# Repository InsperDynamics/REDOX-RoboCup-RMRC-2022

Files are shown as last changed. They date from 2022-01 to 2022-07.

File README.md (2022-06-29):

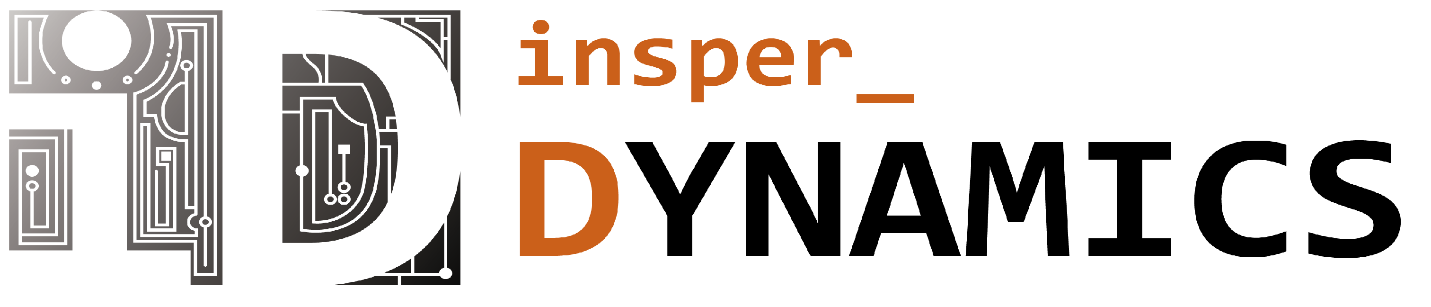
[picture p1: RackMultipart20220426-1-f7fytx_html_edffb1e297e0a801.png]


# Rapidly Manufactured Robot Challenge

# Robocup Rescue 2022

Arthur Martins de Souza Barreto, Enricco Gemha

Felipe Catapano Emrich Melo, Rafael Eli Katri.

April 2022

# Gratitude

Before everything, we want to express our gratitude for some people and organization, without their help we could not achieve everything we already did and still going. In special, Carlos, Felipe Catapano&#39;s father, where he had the initial insight and gave his house for our fist meetings.

We also would like to a huge thank you for our intuition, Insper, they helped us a lot when we need to find a place to train, have our meetings and principally, helped us to pay the cost from our travel to Robocup.

The following names helped us, directly or indirectly, to be the robotics team and build our robot. Thank you, Miranda, Raul, Alicia, Nilson, all laboratorian technical and our family for giving us support.

# About us

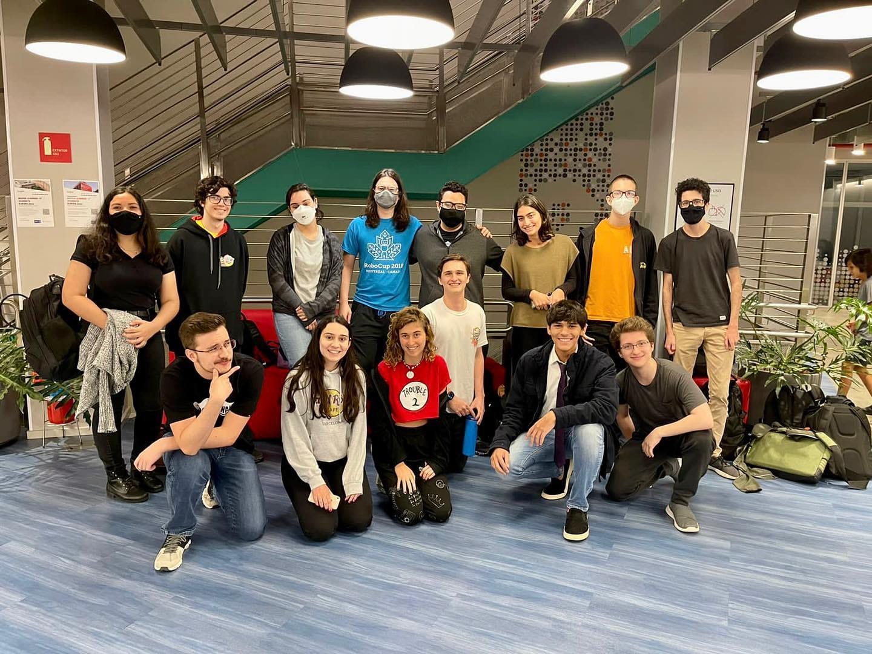
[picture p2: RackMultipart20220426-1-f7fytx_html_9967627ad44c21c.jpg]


We are a Brazilian team, from São Paulo, São Paulo. We born last year, with 3 students from Computer Engineer, two of them already had participate from Robocup, 4 and 2 times respectively, the other is a visionary.

After some hard work we became an official robotics team from our College, Insper, and today we are Insper Dynamics. Our group have students from different courses, Administration, Mechatronics Engineer, Mechanic Engineer, and Computer Engineer. Today we are 15, and still growing up.

## Our Social Medias

- Linkedin:

[https://www.linkedin.com/company/insperdynamics/mycompany/?viewAsMember=true](https://www.linkedin.com/company/insperdynamics/mycompany/?viewAsMember=true)

- Instagram:

[https://www.instagram.com/insper\_dynamics/](https://www.instagram.com/insper_dynamics/)

- Email:

[insperdynamics@gmail.com](mailto:insperdynamics@gmail.com)

- Github:

[https://github.com/InsperDynamics](https://github.com/InsperDynamics)

# Abstract

Our objective is to build a robot capable to get in dangerous ambientes, after natural disasters, places where the human would not be able to go, like a building after an earthquake.

The robot also be able to identify some images to take some actions, if he identifies a symbol of a specific warning, be able to handle it and take the correct action.

The robot is semi-autonomous, at a fist moment he going to be controlled by a remote control, being guide by the image from his camera, and at the same time, he will be mapping the ambient with a laser scanner. With the time pass, he will be able to be autonomous and take his own decision without the human interference.

Also, all the robots were imagined to be fast reproduced, his parts were designed and printed or manufactured, always thinking in how fast we can do it and the better way we can do it.

# Introduction

The world is changing fast, and day after day better solutions comes up. Ten years ago, we had an idea from autonomous cars, self-driving. However, nowadays, we got some cars capable to do that, man is always improving something.

With it in mind, Robocup was born to incentive students under the study from robotics and technology, AI development, everything that would be able to help humankind.

The Rapidly Manufactured Robot Challenge is a category from Robocup, with the goal to build a fast robot make and at the same time, a robot capable to help ser human, going into dangerous places where the man would suffer life risk.

This challenge takes us, Insper Dynamics team to think a lot about some strategies and the results is everything under this paper. For this competition, our team have four members, Arthur, Felipe, Antônio and Rafael, all from 3rd semester at Computer Engineer. The first two students acted as team leaders, teaching everything the group needed, both have 6 participations at Robocup if we some of them. Due we be a new team, we had no teacher helping us yet, but we got great results and have a big expectation on competition.

# Robot

Our robot has all the parts made by us, the body, the arm, the wells, the PCB. The next lines are going to clarify how we imagine and made every part.

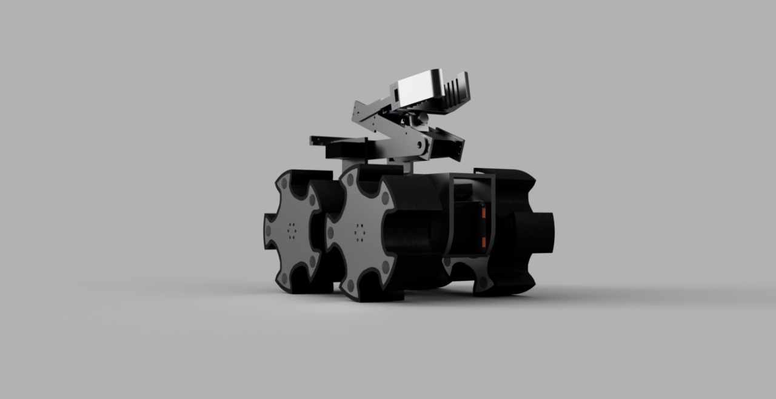
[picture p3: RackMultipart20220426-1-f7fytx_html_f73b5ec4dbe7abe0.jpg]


## Structure

The robot was designed to have two main bodies, independent one from another.

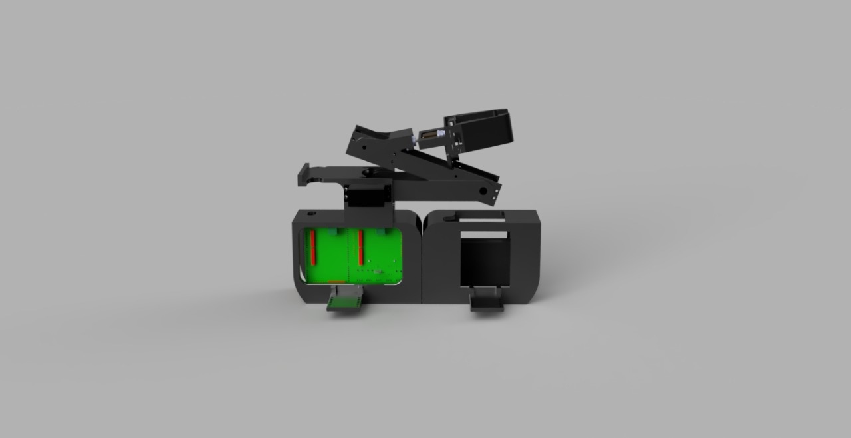
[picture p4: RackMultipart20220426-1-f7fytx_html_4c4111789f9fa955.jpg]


The front and back parts are free to twist around the axis of a central bearing, up to 30 degrees to each side (limited by a cental locking piece). This was done to allow the robot to always have all wheels in contact with the ground. When the robot finds an obstacle that makes a wheel lift, the robot twists, adjusting for the format of the field and continuing its task.

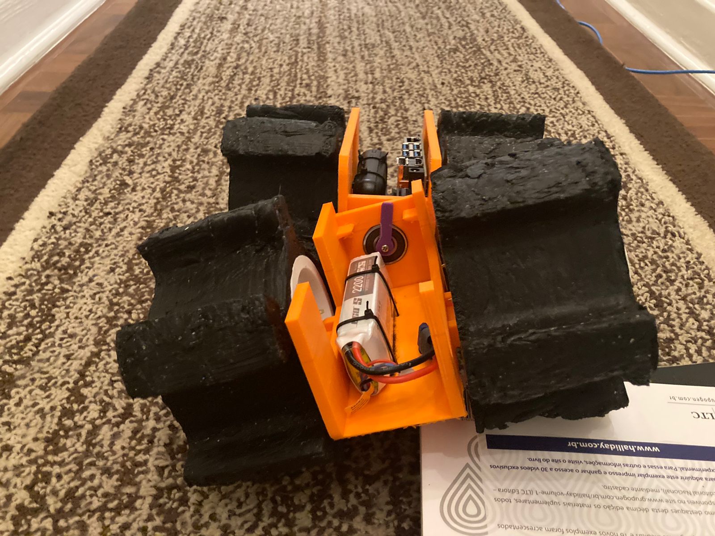
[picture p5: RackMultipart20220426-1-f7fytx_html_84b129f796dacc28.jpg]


On its chassis, we got those two parts, and inside them we placed the following components inside:

- Lipo Battery
- Arduino Mega
- Jetson Nano
- Motor Driver
- Power Bank
- Our PCB

We got two different power sources, one destined for actuators and the other for boards and sensors. This way we avoid interference from low battery under both parts.

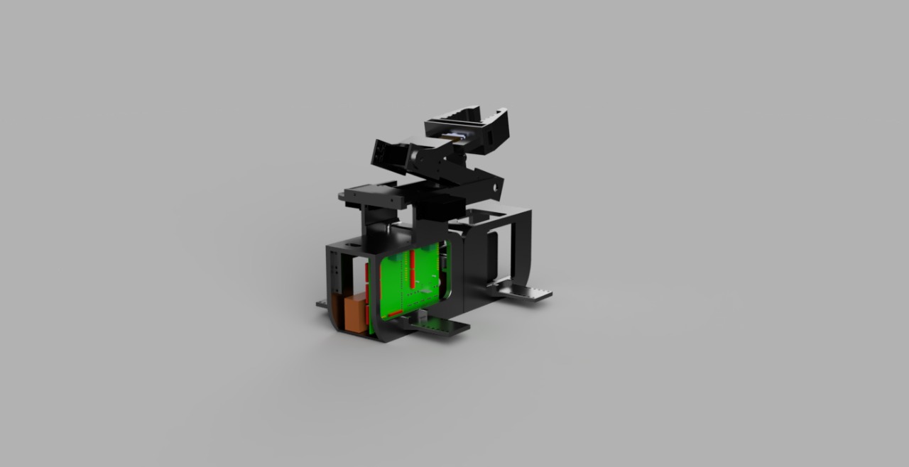
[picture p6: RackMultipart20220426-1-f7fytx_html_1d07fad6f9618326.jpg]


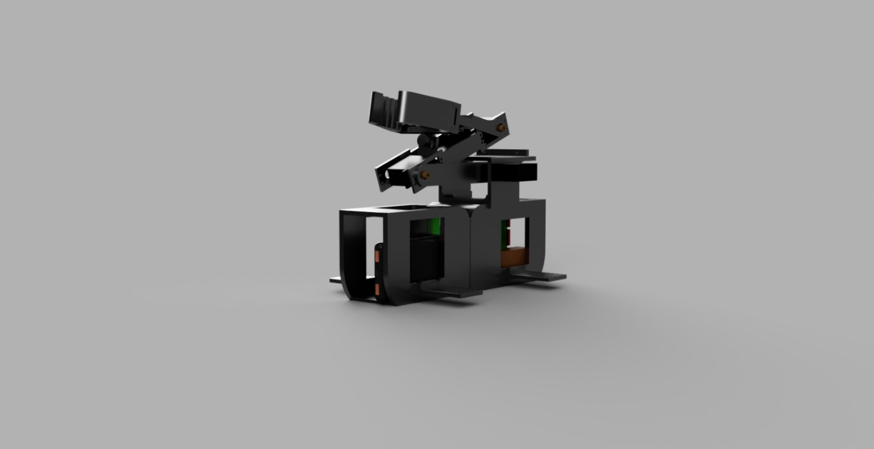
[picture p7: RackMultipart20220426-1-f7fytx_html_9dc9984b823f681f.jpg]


On the body, we have four supports, two at each part. Those supports are going to receive the motors, and after that connect into the wheel.

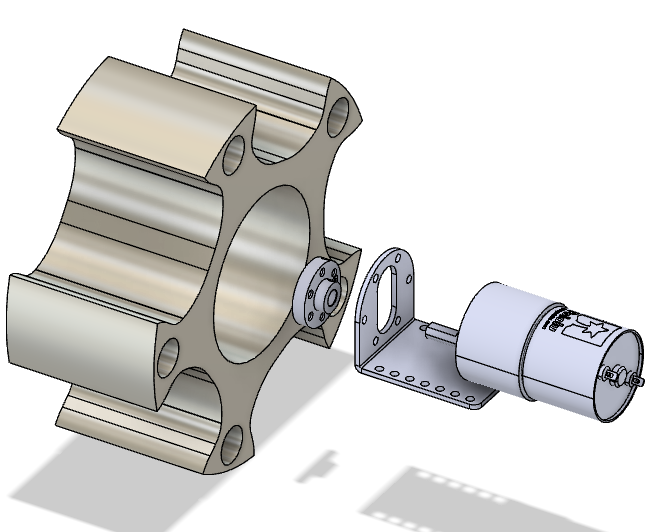
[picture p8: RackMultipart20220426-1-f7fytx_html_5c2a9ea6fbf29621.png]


Furthermore, the robot has an arm, present on the top of the robot. All its parts were 3D-printed and can be downloaded from our repository in GitHub. Chassis STL files and a full model of the robot are also present in the same repository.

The wheels were CNC machined, using equipment from our university. Also, the project can be download at our GitHub page and is free for studying.

The parts discussed above are going to be more clarified on future topics.

### Printing Parts

As one of the main objectives of the RoboCup Rescue RMRC is to develop research across rescue applications, there is a need to create a robot that can be widely spread over different kinds of situations.

Expanding this need, a list of restrictions was created to help our team choose the best material and construction method:

- High impact resistance
- Little flexibility
- Rapid manufacture
- High temperature and fire resistance.

After considering the restrictions made, it was chosen three types of material and 3D printing methods for three stages of development.

The first stage is responsible for the creation of the robot, in which it is made multiple calls between team members to choose which type of robot is better and build different kinds of chassis. In this stage it was used ABS plastic to print beta prototypes of the chassis - In this stage, it was clear that ABS could not be used in the final product as it presented a high flow limit and large deformation in its plastic region.

The second stage was responsible for the development of the chosen chassis and printing of prototypes that simulate the final product (in terms of faithfulness and precision). In this stage, it was used PLA plastic to print the following parts:

- Chassis
- Wheel rim and frame
- Central Bearing Shaft
- Hook

The parts printed presented minimum deformation in its plastic chemical region, good weight resistance but awful resistance to high temperature.

The third stage was responsible for the finalization of development, and production of a function prototype, which used ASA WP filament, provided by 3D Fila (a Brazilian 3D filament company). In this step it was printed the following parts:

- Final Chassis
- Lidar Support
- Camera Support
- Central Bearing Shaft and Limiter
- Hook
- Central support for all the components.

This filament presented good resistance to Wight and deformation - having also the capability of resisting a hostile environment with high UV light and high-temperature exposure.

### Wheels

The robot can move using 4 special wheels designed by the team, arranged in a differential drive setup.

By creating very large (both in width and diameter) profiles with five pickaxe-like surfaces, it was possible to create a drive system that can maneuver on a large variety of terrains and maintain firm contact with the ground. The wheels can naturally &quot;grab&quot; obstacles such as steps and pipes to overcome them, as well as burrow under rocks and sand for better grip.

Unlike threaded designs, this makes them easier to control, as the wheels discard the necessity of arms with additional motors and allow the bearing suspension to be implemented. This way, the robot can always keep four points of contact with the terrain in a passively, self-adapted fashion.

After experimenting with a prototype made with resin and low-infill 3D printing, the team decided to invest on a definitive model for the wheels, based on aluminum and rubber. A CNC machine toolpath with multiple tools was created to replicate more durable and lightweight wheels easily, and support surrounding rubber tires with much higher across all common surfaces.

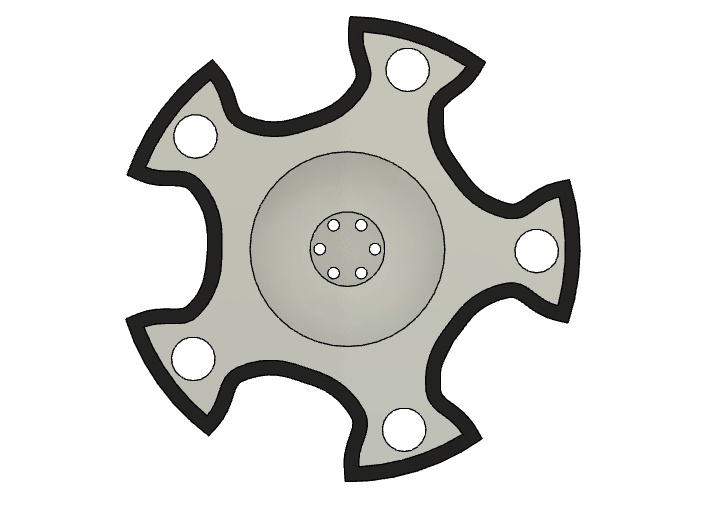
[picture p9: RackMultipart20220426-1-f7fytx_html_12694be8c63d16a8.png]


### Arm

The arm is used to manipulate objects during mobile operation. It has to be able to rotate, extract, precisely touch and allow inspection of relevant features in the environment, that can be positioned in a variety of ways. Therefore, a movable arm was designed from the ground-up to attend those tasks.

Driven by four MG996R and two MG90S servo motors, the arm does not increase the size of the robot (height excluded) when retracted and can reach forward up to two times the chassis length when fully extended. Furthermore, the position of all joints can be controlled independently and precisely.

The end claw has a large, wavy area of contact that can easily attach to objects such as pipe caps. Thanks to two small arc-shaped pieces attached to each finger, it can open and close in a translation-only direction of movement, instead of rotating like human fingers. This is advantageous because the claw can always keep a larger area of contact with the object and evenly distribute the imposing weight.

## Electronics

For the electronics, we started the project with the goal to build our own PCB, and with it, avoid some problems of using cables, bad contacts and all the things that made you crazy at the competition due using cables.

### Motor Drivers

Everyone when get in the robot&#39;s world use the h-bride L298n, super simple to program. However, this h-bride is not efficient energetically, it doesn&#39;t use CMOS technology, and due that have a considerable loss of energy.

To solution this problem we are using another h-bride, a super version from L298n, but using CMOS technology, the VNH2SP30 Dual Driver. This driver can control 2 motors DC, with 30A of current.

We decided to use 4 motors, one at each wheel, so we are using 2 h-bridges to control all of them.

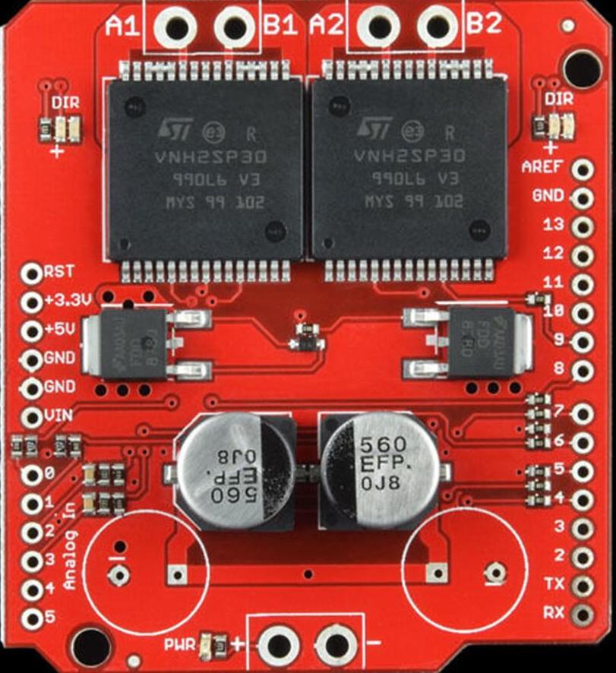
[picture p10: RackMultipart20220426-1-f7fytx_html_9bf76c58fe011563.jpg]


Our version is a shield to Arduino uno&#39;s, as the image above. This motor drive uses the following ports to control the motors:

- Digital 4: InputB from motor 1
- Digital 5: PWM from motor 1
- Digital 6: PWM from motor 2
- Digital 7: InputA from motor 1
- Digital 8: InputA from motor 2
- Digital 9: InputB from motor 2
- Analogic 0: Enable from motor 1
- Analogic 1: Enable from motor 2

The logic from VNH2SP30 is the same as L298n, the only difference is the enable pins, with need to be HIGH to work.

### Voltage Regulator

Our arm works with servo motors, and they are 6 volts. We would need another battery to make the arm work, instead of that we are using a voltage regulator. When we read it under internet, we imagine a 7806 (a simple voltage regulator to 6V).

But previously, we talked about energy efficiency, we this CI is not so efficient, actually, depended on the current, we can have a efficient less 50 %, that would imply a lower life from battery.

To avoid it, we choose the following component, the LM2576.

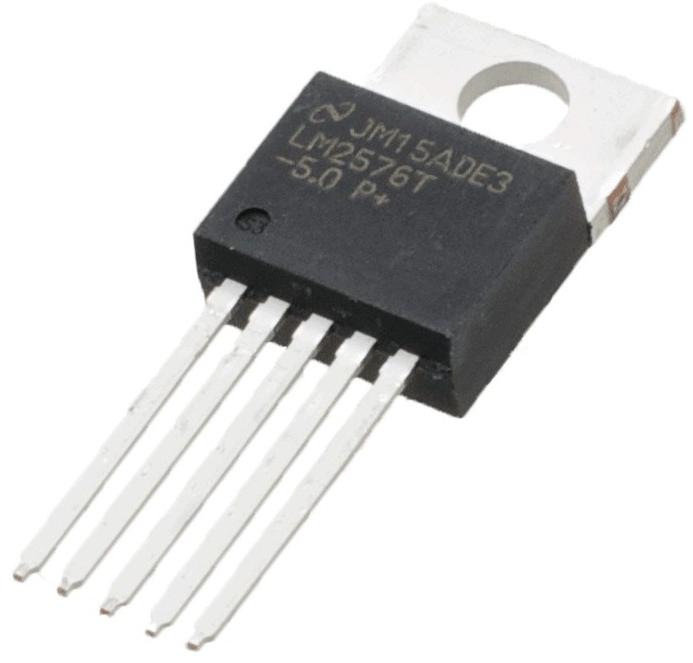
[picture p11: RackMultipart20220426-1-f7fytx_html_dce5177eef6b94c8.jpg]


This component is a regulated voltage tensor, with a higher efficiency. We used the circuit indicated from the fabricant, at DATASHEET.

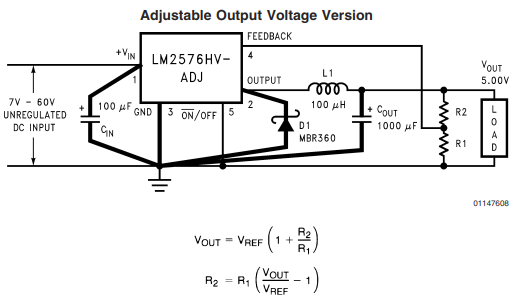
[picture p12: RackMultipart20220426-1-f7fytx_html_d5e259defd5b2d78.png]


View the datasheet at: [https://datasheetspdf.com/pdffile/61720/NationalSemiconductor/LM2576/1](https://datasheetspdf.com/pdffile/61720/NationalSemiconductor/LM2576/1)

###

### PCB

To combine everything and make it simpler to use we projected the PCB to receive the Arduino mega, the voltage regulator circuit, the inputs from the servos, the inputs from CO2 sensor and the thermal camera input.

For project it, we used the software Proteus, with our college gave us the license. Our schematic follows bellow:

In the schematic we can verify 5 regions, two represent the h-bridges, one represents servos inputs and the battery input, the other the Arduino mega input with the sensor and thermal camera and the last, the voltage regulated circuit.

On our first version we had space problems, so we decided to take out the inputs that we were not using from Arduino mega. This way, we got more space to make the lines on board. Also, on the first version, we had a problem with the space to put the inductor and the capacitor from . For simplify it, we put a T-block connection and the problem to put the component was solved. So, we had the following result to the board:

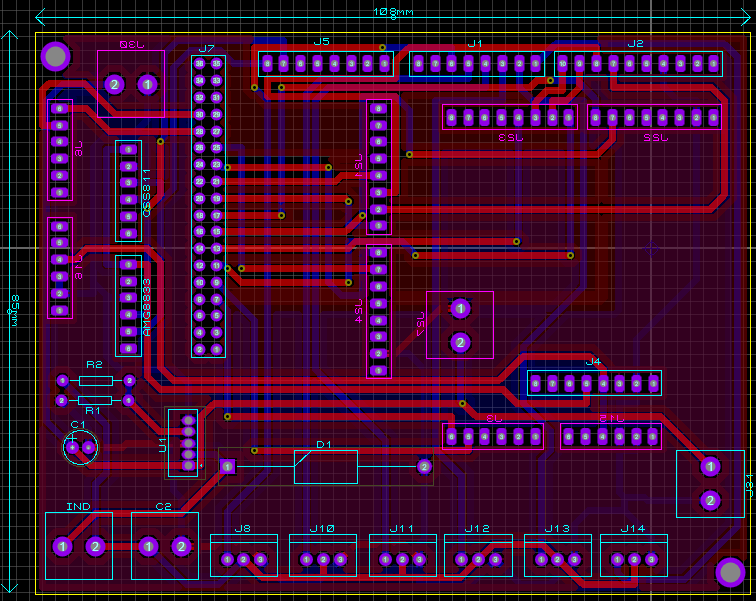
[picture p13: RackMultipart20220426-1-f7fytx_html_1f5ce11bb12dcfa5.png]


To attach on the robot, we put two holes to attach using screw. The board is 2 faced, in another word, it conducts in both sides, the red part conduct at the top, and the blue part conduct at the bottom.

All the inputs from PCB have cables, specially done, for make this connection. On the photos we can see red and black cables. On the board are the cables that support the power of the h-bridges. The other one was to test the boar but are going to receive the battery supply. All the files to make the board can be find at the team github, also you can check pdf from the schematic, bottom, and upper face from the board.

We haven&#39;t mentioned the Jetson Nano yet, but it is used to supply the Arduino, using the serial port. This way, the Arduino is supporting the power for the thermal camera and the CO2 sensor. Besides that, the power bank is responsible to supply the Jetson Nano, this way, we have the control and power parts with different sources.

## Communication

The robot uses two forms for communication, one is for be the bridge between the notebook and the jetson nano, and the last one is used intergrade all the sensor, Arduino with the Jetson Nano.

### VNC

VNC (Virtual Network Computing) is an internet protocol that allows viewing of remote graphical interfaces over a secure connection. In another words, we are going to access Jetson Nano using it, with an ethernet cable.

Download at: [https://www.realvnc.com/pt/connect/download/viewer/](https://www.realvnc.com/pt/connect/download/viewer/)

For this communication, we are using a switch, as the image.



The switch can send and receive data if we use the cable directly on Jetson it would not be possible. At this point, we can access all graphic interface from Jetson only using this switch and an ethernet cable, ready to start the set up and configurations.

### ROS

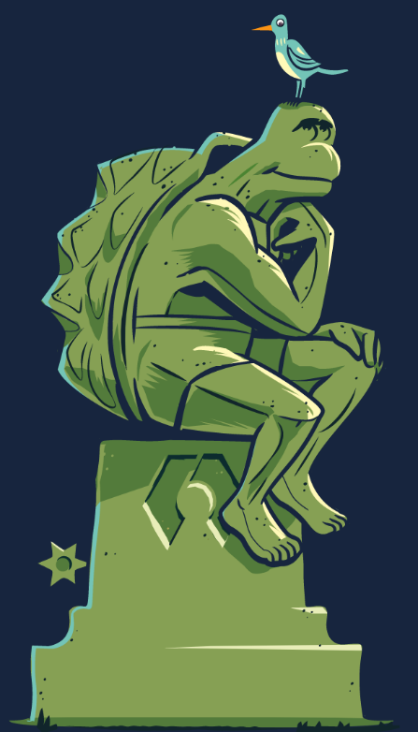
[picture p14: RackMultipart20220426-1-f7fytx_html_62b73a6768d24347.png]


ROS (Robot Operating System) is a tool to make easier and simple the communication between the robot and all the peripherals. Each peripheral can be imagined as a node, and this node something only read, sometimes only write, or can do both. The node can be a sensor, a motor, an Arduino, anything you need, and it is open source. Now more at: [https://www.ros.org](https://www.ros.org/) .

For our robot we are using ROS to make Arduino and jetson communication, everything that is connected on Arduino are receiving order from Jetson and completing their tasks using ROS. Jetson is our central part of communication and responsible from all the actions, read sensor, turn on the motors, everything using ROS. The next lines will clarify how we did it and give you move details how do the same.

## Software Overview

Running software on the robot is divided in 3 parts that operate asynchronously. C++ is utilized for the main code, which is responsible for user interfacing and machine vision algorithms, utilizing OpenCV, as well as communicating with the Arduino via ROS-Serial.

The Arduino board´s code is responsible for low-level interfacing of motors, thermal sensor, and gas sensor with PWM and I2C communication protocols. This is uploaded to the board via the Arduino IDE installed on the main board. Lastly, a set of Python scripts is used to launch base ROS nodes and handling input from the Lidar and Realsense sensors. These are manifested by the laser\_scan and odometry-related topics respectively.

The team used Visual Studio Community, Visual Studio Code and Sublime Text 3 during the developed of all self-made scripts used by the robot.

### Setup

To evaluate and run the software, a few dependencies have to be present on the target environment. The team recommends the utilization of Ubuntu 18.04LTS as the operating system for all steps.

Firstly, the user is required to install ROS on their machine. More instructions on this task can be found at [http://wiki.ros.org/ROS/Installation](http://wiki.ros.org/ROS/Installation) (for Ubuntu 18.04, the Melodic Morenia distribution is recommended). This is the middleware required for all virtual nodes to communicate.

Additionally, OpenCV, ZBar and SDL are required for the main portion of the software to execute correctly.

Arduino IDE should be installed to manage and upload code to the Arduino Mega. Instructions to do this on Linux machines can be found at [https://docs.arduino.cc/software/ide-v1/tutorials/Linux](https://docs.arduino.cc/software/ide-v1/tutorials/Linux). Lastly for dependencies, the user can install SoX to transmit input from the robot´s microphone to the operator in real time.

To run the team´s code, use git to clone the repository at [https://github.com/InsperDynamics/REDOX-RoboCup-RMRC-Challenge](https://github.com/InsperDynamics/REDOX-RoboCup-RMRC-Challenge).

The Arduino\_Side folder contains software to be uploaded via ArduinoIDE, all necessary external libraries can be installed via library manager. They are: rosserial (version 0.7.9), Adafruit_AMG88xx (any version) and Adafruit_CCS811 (any version).
The main C++ software is found at Machine Vision and should be compiled via g++. Use catkin\_make command to build necessary ROS packages prior to launching the interface.

 A bash file is included in order to automatically install all of the necessary dependencies on a Jetson Nano device with a fresh installation of the official JetPack OS.

To access the robot via VNC, the team recommends the usage of VNC Viewer. The instructions on this page can be used to find the IP address of the main board: [https://help.ubuntu.com/stable/ubuntu-help/net-findip.html.en](https://help.ubuntu.com/stable/ubuntu-help/net-findip.html.en). In case of difficulties while trying to forward input from the gamepad to the VNC server, the user can use USB/IP (install and setup instructions at [http://usbip.sourceforge.net/](http://usbip.sourceforge.net/) ).

### Jetson Nano

The Nvidia Jetson Nano 4gb Developer Kit was chosen to be used as the main processing unit of the robot, and is responsible for communicating with the Arduino, high-level sensors, and operator machine, as well as running the machine vision algorithms and organizing autonomous movement.

Designed for machine learning and dynamic robotics in mind, it contains a 128-core NVIDIA Maxwell™ architecture-based GPU, a Quad-core ARM CPU, 4gb of LPDDR4 RAM and has support for Linux for Tegra. All on a compact (100mm x 80mm) and affordable package. It also contains 4 USB-3 ports, gigabit ethernet, a CSI port and GPIO. This makes it very suitable for running all necessary processes required for operation in parallel, while being powered with 5V via micro-USB.

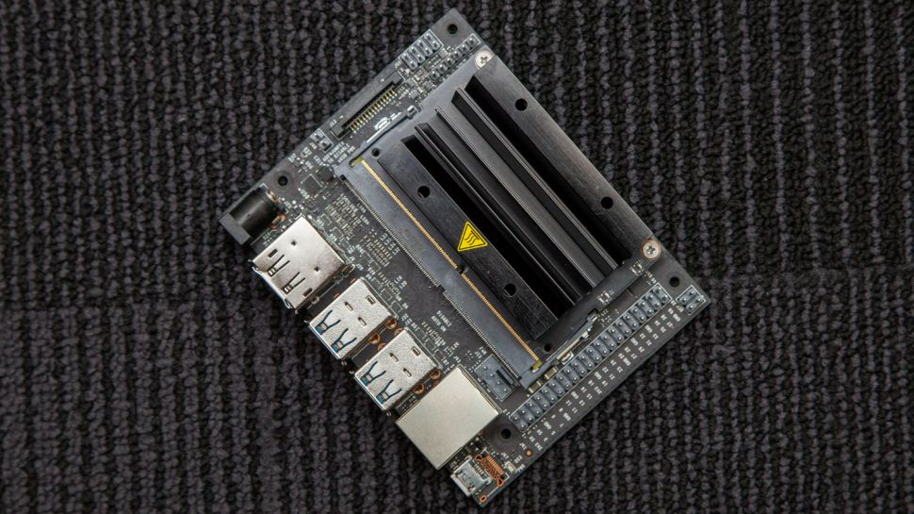
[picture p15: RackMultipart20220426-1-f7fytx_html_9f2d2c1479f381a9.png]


### Sensors

The competition has two specific task that need an external sensor, one is to show a thermal image from the place and the other is to show the concentration of CO2.

Their connections with the Arduino can be checked at the schematic from PCB, some explanations will be given on the next lines. Also, is important say that both only use 4 pins to work, as showed at schematic, 2 for supply and 2 for communication.

#### Thermal Camera

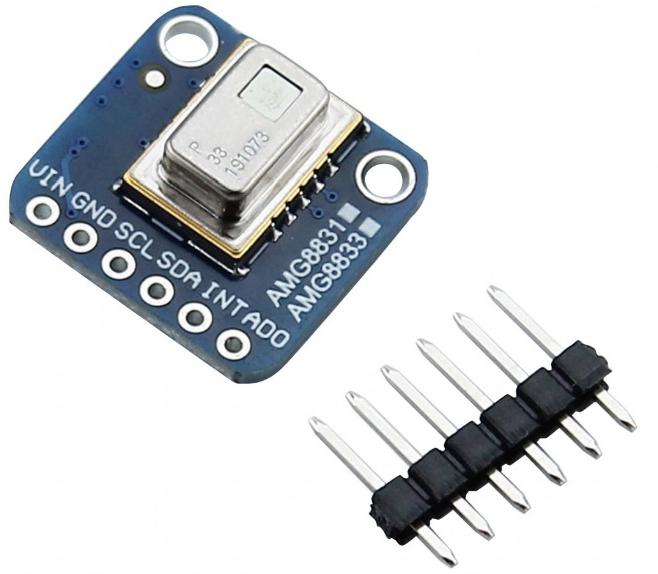
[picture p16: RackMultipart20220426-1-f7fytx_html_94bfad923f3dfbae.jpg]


The thermal camera which we are using is the AMG8831, that has support for Arduino, raspberry and other with I2C communication. This electronic module has and high efficiency and is based on Infrared heat detection sensor that allows the user to detect movement in dark environments, for example.

This sensor has a matrix of 8x8 thermal sensors, and returns a matrix of 64 temperature individual reading, and has a work like a professional thermal camera.

It can identify temperature between 0ºC to 80ºC, also has and precision of . This module works with , that comes from Arduino, and is connected on SDA and SCL pins from Arduino mega. This sensor represents a node from ROS, making everything more simple and easier to organize on coding.

Know more at: [https://learn.adafruit.com/adafruit-amg8833-8x8-thermal-camera-sensor](https://learn.adafruit.com/adafruit-amg8833-8x8-thermal-camera-sensor) .

#### CO2

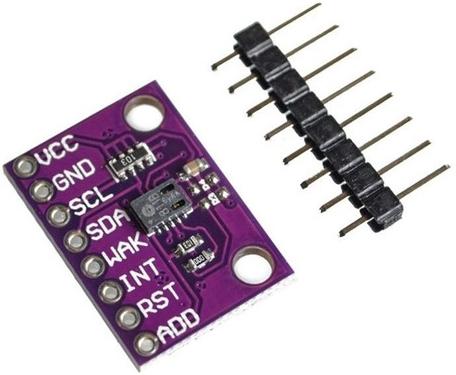
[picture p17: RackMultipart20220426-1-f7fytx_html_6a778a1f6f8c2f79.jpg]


The CCS811 is a low power miniature digital gas sensor for monitoring air quality. A metal oxide sensor is integrated to measure the total volatile organic compounds equivalent of TVOCs, making it possible to monitor air quality when working in conjunction with microcontrollers, only requiring I2C serial communication.

The module is based on unique microplate technology, meaning the plate presents a highly reliable solution for projects that require gas sensor, fast cycle times and a significant reduction in average power consumption. The integrated MCU manages the sensor trigger modes and the measured data.

The CCS811 supports intelligent algorithms to process measurements and output an equivalent TVOC value, as well as supporting multiple measurement modes that are optimized for low power consumption, thus extending battery life in portable devices.

He also requires of power and comes from Arduino. His pins from CLOCK and DATA (SCL and SDA) are connected in series with the same pins from the thermal camera, and them connected on Arduino&#39;s I2C pins.

Learn more at: [https://www.sparkfun.com/products/14193](https://www.sparkfun.com/products/14193) .

### Lidar

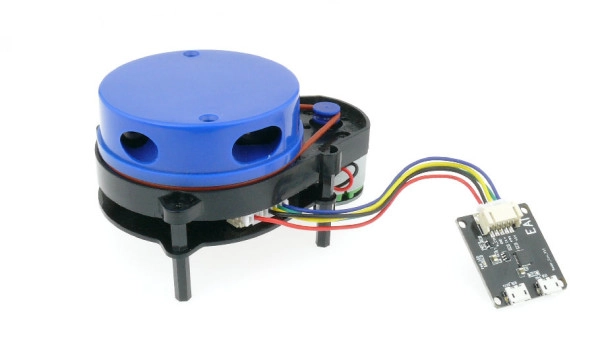
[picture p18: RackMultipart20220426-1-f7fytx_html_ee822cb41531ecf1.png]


Autonomous mapping is achieved using a compact rotating laser distance sensor module, mounted on top of the chassis. This is very useful not only for autonomous movement planning, but also for localizing the robot in relation to features present in the map without getting lost. The YDLidar X4 is a low-cost solution for measuring distances of 12 centimeters up to 10 meters, in two dimensions.

Lidar stands for light detection and ranging and uses pulsed laser light to measure the distance to an object. The laser is reflected off the surface of the object, and the distance to the object is determined by measuring the time it takes for the light to reach the sensor. Typically, lasers are chosen that use wavelengths of light outside the visible spectrum, usually infrared.

Power is supplied directly to the module via USB, and a second port is connected to the power bank present on the robot for the event of power supply insufficiency.

Since official drivers and ROS package support exists, interfacing with the lidar is a rather simple task. It is worth noting, however, that in the case of our robot, the module is placed upside down to avoid making the scan plane sit above the top plane of the arena walls when traversing large obstacles. Because of this, an inverted transform data is used for accurate scanning in the software.

### Realsense T265

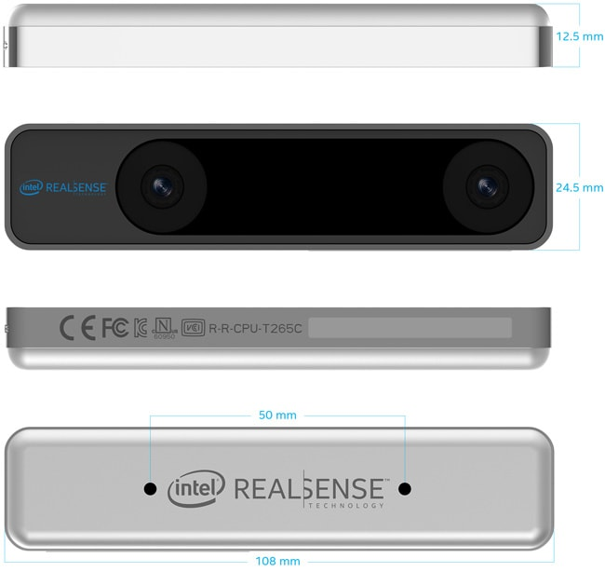
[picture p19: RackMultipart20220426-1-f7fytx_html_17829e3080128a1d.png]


For the front camera of the robot, an Intel Realsense T265 tracking camera was used. This module combines two OV9282 imagers with fisheye lenses, a BMI055 IMU and an Intel® Movidius™ Myriad™ 2.0 visual processing unit to deliver Visual Inertial Odometry.

Designed to work both indoors and outdoors, the camera can automatically triangulate visual features in the environment to obtain positional information that gets published to our ROS ecosystem. It helps to mitigate drift generated from Lidar-only SLAM and increase mapping confidence, even if the robot is suddenly transported from one part of the arena to another.

The wide FOV also benefits teleoperation and human control. With 163 degrees globally, the operator can have a better understanding on what is in front, above, below or on the sides the robot while moving quickly, securing pose data at the same time. By applying an anti-distortion algorithm, it also provides enough image resolution for detection of far away objects.

The only encountered downside by the team is the fact that this camera can only output images in grayscale. For color recognition, other cameras present on the robot should be used instead.

### Other Cameras

Along with the Realsense unit, the robot contains a back camera and a claw camera. Both can output colored images at 1080p resolution.

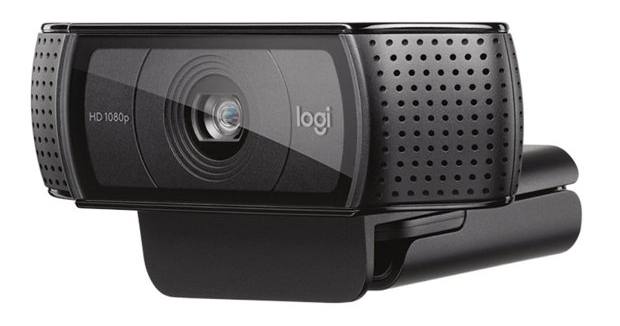
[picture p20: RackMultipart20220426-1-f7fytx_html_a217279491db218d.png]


On the back, a Logitech C920 webcam is used to transmit video feed when operating in backwards motion. This is very helpful in scenarios where the robot reaches a dead-end and must return, preferably without having to turn around its own axis, something that happens constantly in RMRC. It was chosen due to its high resolution at 30 frames per second, ability to automatically adjust focus, contrast and saturation (this is achieved by RightLight 2 technology), and good FOV (78 degrees horizontally).

The C920 is also used for the audio input of the robot thanks to the two omnidirectional microphones connected to the same port of its imager.

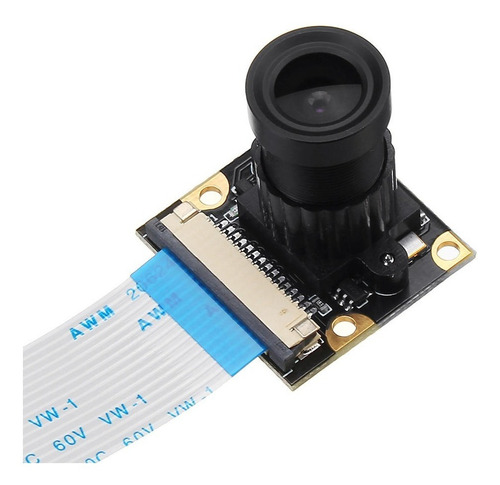
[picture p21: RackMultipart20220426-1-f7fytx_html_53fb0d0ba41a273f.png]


For arm operation/inspection, an Ov5647 is attached to a support sitting above the robot´s claw. It is a small camera with 60 degrees of horizontal FOV, that takes advantage of the CSI camera port present on the left side of the Jetson Nano.

### Object Detection

Regarding object detection, the robot can detect hazmat, QR codes and motion.

To implement hazmat detection, we firstly tried to create our own model. With this objective, we gathered a dataset composed of 14 categories and started to annotate the images with Pascal-VOC to train a Yolo V4 based model. Unfortunately, we had a setback; our hardware was not good enough to train a proper model and our time was short to manually annotate the 2000+ images.

In the meantime, we found Mobile Robotics Laboratory&#39;s YOLO V3-tiny, based model, [DeepHAZMAT](https://github.com/mrl-amrl/DeepHAZMAT), as a replacement for our model. This open-source model was thoroughly crafted using real life hazmat signs, photographed form multiple angles. OpenCV, a computer vision library, reads both weight and configuration files of the model, constantly checking the input image for potential hazmat and keeping score of their confidence levels. This model&#39;s dataset is made of 13 labels, detailed hereafter:

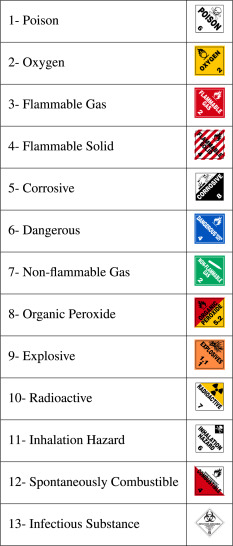
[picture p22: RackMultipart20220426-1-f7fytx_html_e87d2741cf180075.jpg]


Additionally, a non- maximum suppression algorithm filters the best candidates of the frame, as the areas surrounding hazmats tend to trigger the model with a lower score.

Motion detection is achieved via frame difference extraction. Each new obtained frame is subject to a Gaussian blur filter, a frame delta is then calculated, filtered and dilated. OpenCV´s findContours() method is then used to find all highlighted blobs in the delta frame, which get filtered by height-width ratio before being draw on screen.

The previously stated approach has proven to be very effective for detecting small, rapidly moving objects, especially high-contrast blobs, hence why we adopted it for RMRC black dot detection.

As for QR code detection, ZBar&#39;s bar code reading C++ library was used to detect QR codes on each frame. Both forms of object detection have visual representation on the interface.

### Interface

The graphical user interface utilized by the operator was entirely built in C++, utilizing OpenCV to handle all windows. It is designed for minimum complexity and ease of use since the team opted for a dual-monitor approach. Almost all controls are handled via gamepad, which is autodetected by the program, leaving only what is necessary for operation visible to the operator.

Most of the left monitor area is utilized by the current camera feed, which can be switched via the L/R buttons on the gamepad. On the upper left corner, the thermal camera feed is formed in real time, with each pixel ranging from a dark blue tone to red, according to its reading, and then upscaled. Similarly, a large yellow line is formed underneath to indicate the measured level of CO2 concentration in front of the robot.

On the right-hand side, a set of sliders is spawned for control of the arm claw. The position of each servo motor can be directly controlled with a mouse, this allows the operator to use its entire arm to precisely manipulate each joint. In contrast, moving the robot wheels is entirely based on analog joystick output, so that different velocity states can be input quickly.



The other attached monitor should be used to render Rviz or a similar visualization (e.g., Cartographer) program during operation. This is additional feedback regarding estimated states of the robot and can be useful to ensure that the robot is moving properly and mapping the environment as intended, as well as calculated trajectory, for autonomous operation. A single button on the gamepad is used to alternate between manual and autonomous control, and another for turning image post-processing on or off.

### Autonomous Part

An autonomous mode is available, which allows the robot to simultaneously map the environment, keep track of its position and control its trajectory. This is achieved using ROS&#39;s _gmapping_ and _move\_base_ packages.

Gmapping is a package that runs a simultaneous localization and mapping (SLAM) algorithm. Its only node, _slam\_gmapping_, constantly updates a map (OccupancyGrid) and the robot&#39;s position within it. The requirements of the SLAM algorithm are Lidar&#39;s laser scan input, Realsense&#39;s odometry data and the required _tf transformations_ for both sensors.

As the sensors are placed in different positions of the robot, a reference point must be defined to successfully organize its movement, which is called base link. With this matter in mind, a tf transformation is used to create an offset to the values of a sensor, associating the information to base link. The required transformations are base\_link ←Scan, which set a base\_link point based on lidar&#39;s data, odom ← base\_link, which corrects Realsense&#39;s odometry value to base link&#39;s position, and map ← odom, which associates the robot&#39;s position to a fixed reference point of the map.

While _slam\_gmapping_ is running, both map&#39;s OccupancyGrid and transformation are constantly updated. From this data a goal pose is calculated, also associated with the map&#39;s fixed reference point, and subscribed by _move\_base._ Afterward, _move\_base_ publishes to /cmd\_vel the velocity needed to assure that the robot follows the desired trajectory.

## Costs

Everything used on the robot is listed on the following table, everything is on the Brazilian coin, on the end we converted it do American Dolar for possible future comparation between the other teams.

| Component | Amount | Unitary Cost (BRL) | Total Cost (BRL) |
| --- | --- | --- | --- |
| CO2 Sensor: CCS811 | 1 | R$ 80,00 | R$ 80,00 |
| Thermal Camera: AMG8833 | 1 | R$ 240,00 | R$ 240,00 |
| VNH2SP30 Dual Driver | 2 | R$ 130,00 | R$ 260,00 |
| Arduino Mega 2560 | 1 | R$ 140,00 | R$ 140,00 |
| Servo Motor MG996R | 4 | R$ 35,00 | R$ 140,00 |
| Servo Motor MG90S | 2 | R$ 25,00 | R$ 50,00 |
| Nvidea Jetson Nano 4gb Developer Kit | 1 | R$ 1400,00 | R$ 1400,00 |
| Intel Realsense T265 | 1 | R$ 2165,00 | R$ 2165,00 |
| Ethernet Cable (15 m) | 1 | R$ 30,00 | R$ 30,00 |
| Camera Ov5647 1080p | 1 | R$ 130,00 | R$ 130,00 |
| 70:1 Metal Gearmotor 37Dx54L mm 12V (Helical Pinion) | 4 | R$ 155,00 | R$ 620,00 |
| Camera Logitech C920 | 1 | R$ 370,00 | R$ 370,00 |
| YDlidar X4 | 1 | R$ 1200,00 | R$ 1200,00 |
| PowerBank 20.000 mAh | 1 | R$ 115,00 | R$ 115,00 |
| PLA Filament (500 g) | 2 | R$ 85,00 | R$ 170,00 |
| Dualsky Eco S 12V 2200mAh LiPo battery | 1 | R$ 115,00 | R$ 115,00 |
| Dual faced Custom PCB | 1 | R$ 430,00 | R$ 430,00 |
| Bearing 6201 Ddu C3 12x32x10 | 1 | R$ 20,00 | R$ 20,00 |
| Xbox 360 Controller | 1 | R$ 60,00 | R$ 60,00 |
| TP-Link LS1005G LiteWave | 1 | R$ 105,00 | R$ 105,00 |

Total Cost is R$ 7840,00, in American dollar is $ 1.662,50. Note, the conversion between the coins were made in April, so it can change when you are reading this paper.

# Future Upgrades

Although the team was satisfied with the overall design of the robot for this edition, a few improvements could be made. These aim to obtain maximum efficiency while keeping its principles, to better attend both the general needs for real rescue scenarios, as well as more specific tasks of RoboCup Rescue.

Firstly, the project could greatly benefit from wireless connectivity. By utilizing a high-range antenna attached to the main board, the necessity of a cable manager on the operation site would be eliminated. This not only reduces human injury risks, but also removes the constraint of the ethernet cable itself, which can tangle, twist or even break depending on the environment.

High-level machine vision and ROS algorithm processing can also be shifted to the operator´s computer. This way, the robot could be redesigned to only comport sensors and lower-level components that we can design, without the need for an onboard GPU for example. The result would be a permission to reduce weight and size of the robot, as well as keeping the high-level source code on a PC for easier access and security.

The arm could also be improved with the utilization of servo units that benefit from daisy-chain technology. Models such as the DRS - 0101 HerkuleX Smart Servo can connect to one another reducing the total amount of wiring on the robot, as well as offering trapezoidal velocity profile, PID and other useful algorithms for precise control applied automatically.

Finally, the team recognizes that higher-resolution thermal imaging sensors and 3D scanning capabilities are more well-suited for real rescue scenarios. Unfortunately, no alternatives that would not significantly increase the cost of the robot were found by the team yet.

# How to setup a VNC connection 

## For reference:

* OS: Ubuntu 20.04.3 LTS
* VNC Server library: Vino (OBS: It is GNOME based)
* VNC Client: VNC viewer

## Commands that manage Vino's settings (Run once):

```
sudo apt-get install vino

gsettings set org.gnome.Vino require-encryption false

gsettings set org.gnome.Vino propmpt-enabled false

gsettings set org.gnome.Vino authentication-methods "[vnc]"

gsettings set org.gnome.Vino vnc-password $(echo -n 'insertPasswordHere'|base64)
```

## Commands to start VNC Server (Run always):

* To get the correct IP address:

```
hostname -I
```

* To start Vino:

```
/usr/lib/vino/vino-server
```

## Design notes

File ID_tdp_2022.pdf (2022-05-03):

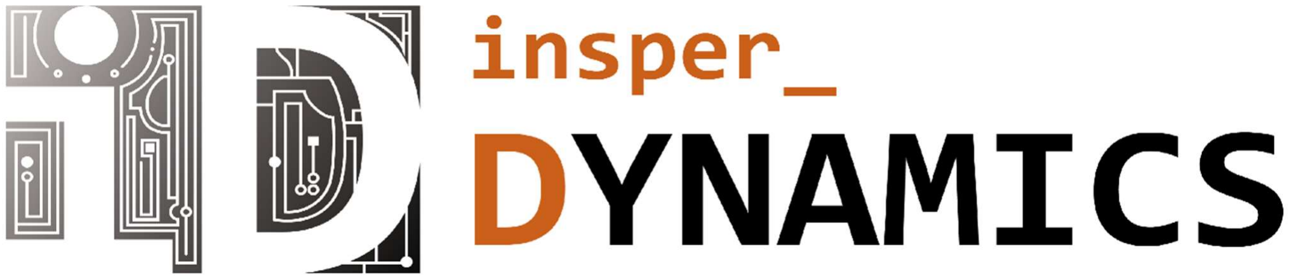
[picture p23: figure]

## Team Description Materials

## Rapidly Manufactured Robot Challenge

## Robocup Rescue 2022

Antônio Amaral Egydio Martins, Arthur Martins de Souza Barreto,

Felipe Catapano Emrich Melo, Rafael Eli Katri.

April 2022

## Summary

3

### Gratitude

Before everything, we want to express our gratitude for some people and organization, without their help we could not achieve everything we already did and still going. In special, Carlos, Felipe Catapano’s father, where he had the initial insight and gave his house for our fist meetings.

We also would like to a huge thank you for our intuition, Insper, they helped us a lot when we need to find a place to train, have our meetings and principally, helped us to pay the cost from our travel to Robocup.

The following names helped us, directly or indirectly, to be the robotics team and build our robot. Thank you, Miranda, Raul, Alicia, Nilson, all laboratorian technical and our family for giving us support.

### About us

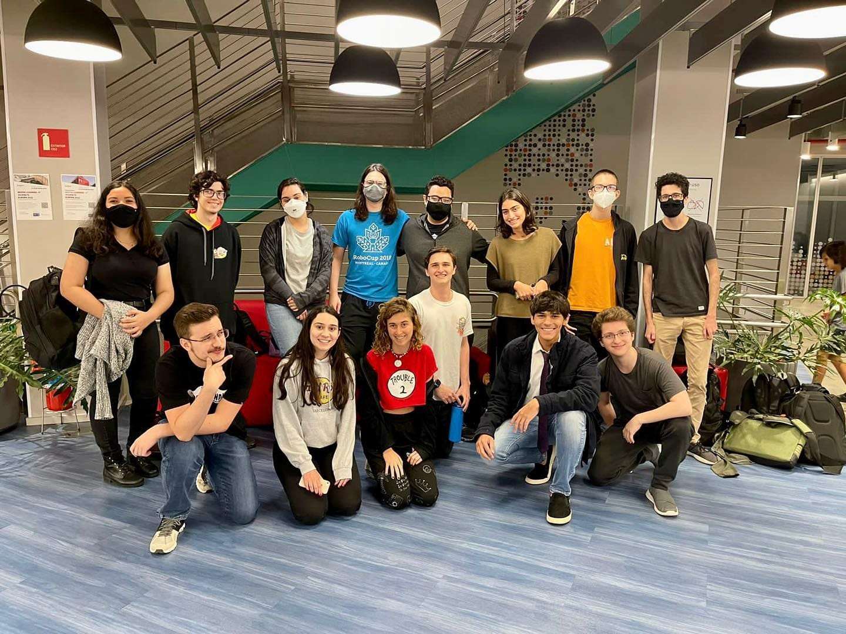
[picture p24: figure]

4

We are a Brazilian team, from São Paulo, São Paulo. We born last year, with 3 students from Computer Engineer, two of them already had participate from Robocup, 4 and 2 times respectively, the other is a visionary.

After some hard work we became an official robotics team from our College, Insper, and today we are Insper Dynamics. Our group have students from different courses, Administration, Mechatronics Engineer, Mechanic Engineer, and Computer Engineer. Today we are 15, and still growing up.

Our Social Medias

- Linkedin:

https://www.linkedin.com/company/insperdynamics/mycompany/?viewAsMember=true

- Instagram:

https://www.instagram.com/insper_dynamics/

- Email:

insperdynamics@gmail.com

- Github:

https://github.com/InsperDynamics

### Abstract

Our objective is to build a robot capable to get in dangerous ambientes, after natural disasters, places where the human would not be able to go, like a building after an earthquake.

The robot also be able to identify some images to take some actions, if he identifies a symbol of a specific warning, be able to handle it and take the correct action.

5

The robot is semi-autonomous, at a fist moment he going to be controlled by a remote control, being guide by the image from his camera, and at the same time, he will be mapping the ambient with a laser scanner. With the time pass, he will be able to be autonomous and take his own decision without the human interference.

Also, all the robots were imagined to be fast reproduced, his parts were designed and printed or manufactured, always thinking in how fast we can do it and the better way we can do it.

### Introduction

The world is changing fast, and day after day better solutions comes up. Ten years ago, we had an idea from autonomous cars, self-driving. However, nowadays, we got some cars capable to do that, man is always improving something.

With it in mind, Robocup was born to incentive students under the study from robotics and technology, AI development, everything that would be able to help humankind.

The Rapidly Manufactured Robot Challenge is a category from Robocup, with the goal to build a fast robot make and at the same time, a robot capable to help ser human, going into dangerous places where the man would suffer life risk.

This challenge takes us, Insper Dynamics team to think a lot about some strategies and the results is everything under this paper. For this competition, our team have four members, Arthur, Felipe, Antônio and Rafael, all from 3rd semester at Computer Engineer. The first two students acted as team leaders, teaching everything the group needed, both have 6 participations at Robocup if we some of them. Due we be a new team, we had no teacher helping us yet, but we got great results and have a big expectation on competition.

### Robot

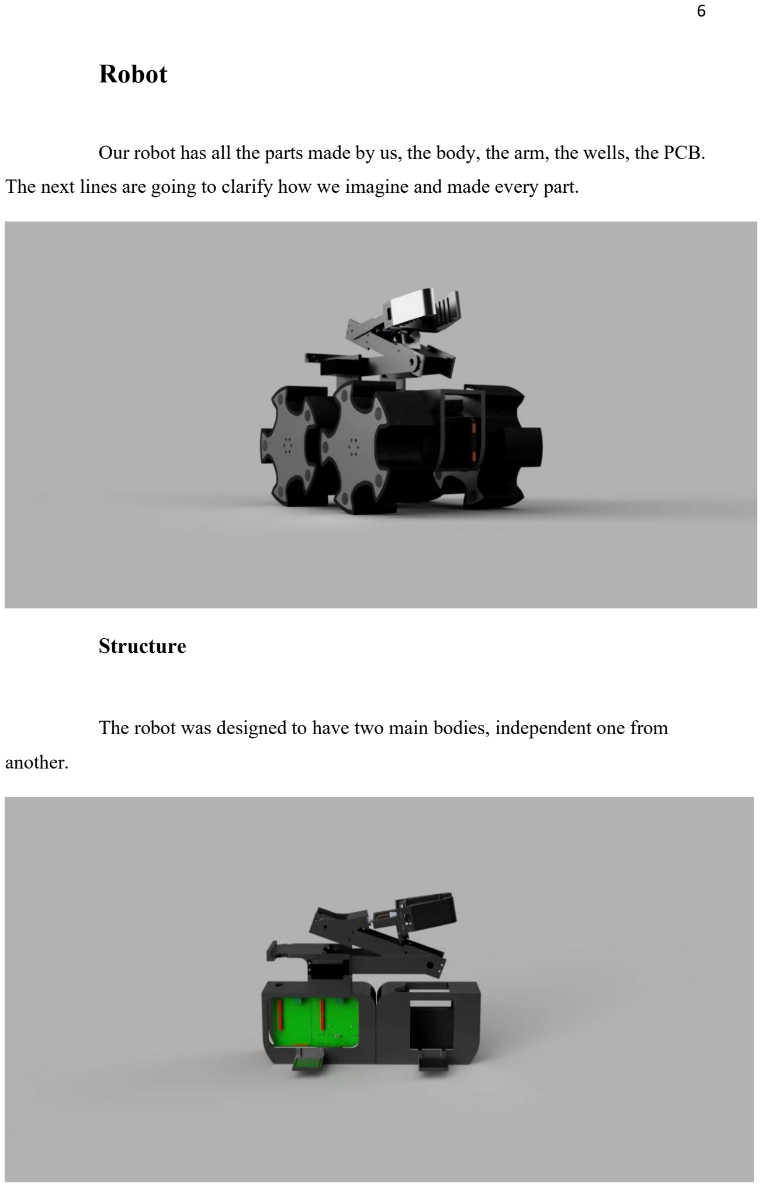
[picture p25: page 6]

6

Our robot has all the parts made by us, the body, the arm, the wells, the PCB. The next lines are going to clarify how we imagine and made every part.

Structure

The robot was designed to have two main bodies, independent one from another.

7

The front and back parts are free to twist around the axis of a central bearing, up to 30 degrees to each side (limited by a cental locking piece). This was done to allow the robot to always have all wheels in contact with the ground. When the robot finds an obstacle that makes a wheel lift, the robot twists, adjusting for the format of the field and continuing its task.

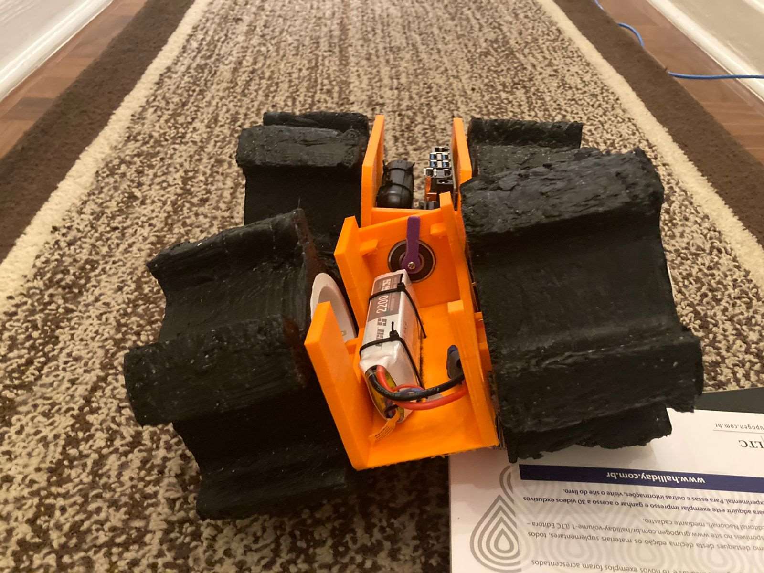
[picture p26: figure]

On its chassis, we got those two parts, and inside them we placed the following components inside:

- Lipo Battery
- Arduino Mega
- Jetson Nano
- Motor Driver
- Power Bank
- Our PCB

We got two different power sources, one destined for actuators and the other for boards and sensors. This way we avoid interference from low battery under both parts.

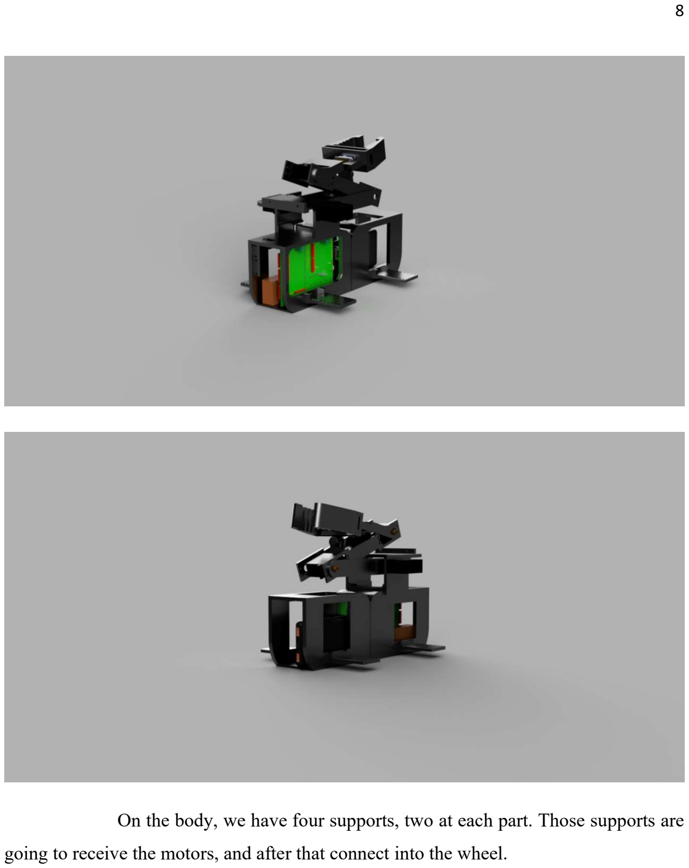
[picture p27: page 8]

8

On the body, we have four supports, two at each part. Those supports are going to receive the motors, and after that connect into the wheel.

9

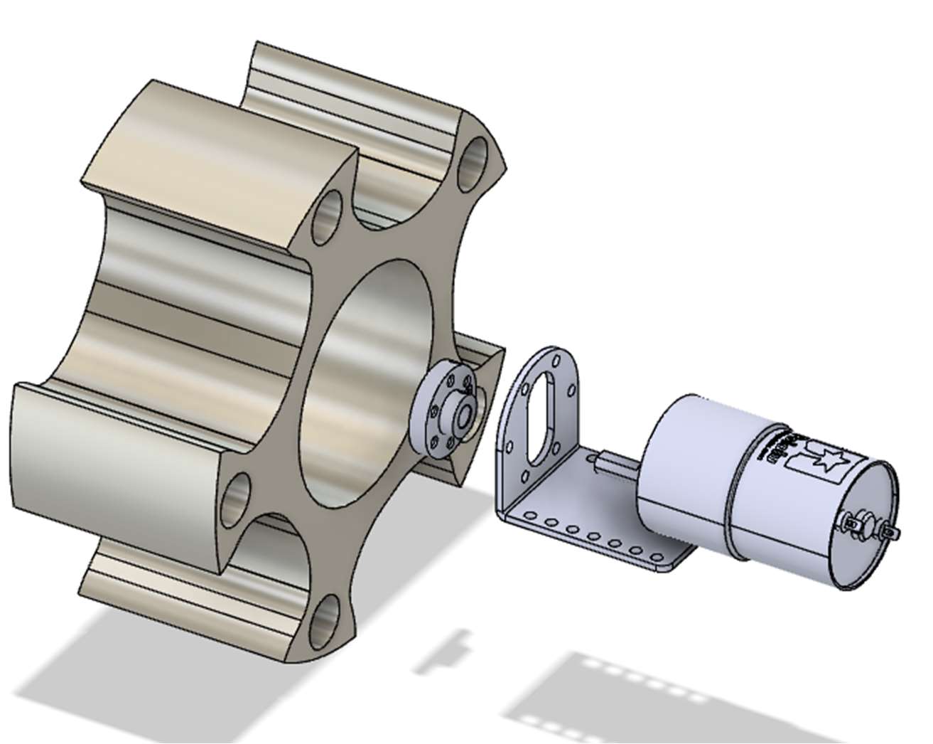
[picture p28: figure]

Furthermore, the robot has an arm, present on the top of the robot. All its parts were 3D-printed and can be downloaded from our repository in GitHub. Chassis STL files and a full model of the robot are also present in the same repository.

The wheels were CNC machined, using equipment from our university. Also, the project can be download at our GitHub page and is free for studying.

The parts discussed above are going to be more clarified on future topics.

Printing Parts

As one of the main objectives of the RoboCup Rescue RMRC is to develop research across rescue applications, there is a need to create a robot that can be widely spread over different kinds of situations.
Expanding this need, a list of restrictions was created to help our team choose the best material and construction method:
- High impact resistance
- Little flexibility
- Rapid manufacture
- High temperature and fire resistance.

10

After considering the restrictions made, it was chosen three types of material and 3D printing methods for three stages of development.
The first stage is responsible for the creation of the robot, in which it is made multiple calls between team members to choose which type of robot is better and build different kinds of chassis. In this stage it was used ABS plastic to print beta prototypes of the chassis - In this stage, it was clear that ABS could not be used in the final product as it presented a high flow limit and large deformation in its plastic region.
The second stage was responsible for the development of the chosen chassis and printing of prototypes that simulate the final product (in terms of faithfulness and precision). In this stage, it was used PLA plastic to print the following parts:
- Chassis
- Wheel rim and frame
- Central Bearing Shaft
- Hook

The parts printed presented minimum deformation in its plastic chemical region, good weight resistance but awful resistance to high temperature.
The third stage was responsible for the finalization of development, and production of a function prototype, which used ASA WP filament, provided by 3D Fila (a Brazilian 3D filament company). In this step it was printed the following parts:
- Final Chassis
- Lidar Support
- Camera Support
- Central Bearing Shaft and Limiter
- Hook
- Central support for all the components.

This filament presented good resistance to Wight and deformation - having also the capability of resisting a hostile environment with high UV light and high-temperature exposure.

11

Wheels

The robot can move using 4 special wheels designed by the team, arranged in a differential drive setup.

By creating very large (both in width and diameter) profiles with five pickaxe-like surfaces, it was possible to create a drive system that can maneuver on a large variety of terrains and maintain firm contact with the ground. The wheels can naturally “grab” obstacles such as steps and pipes to overcome them, as well as burrow under rocks and sand for better grip.

Unlike threaded designs, this makes them easier to control, as the wheels discard the necessity of arms with additional motors and allow the bearing suspension to be implemented. This way, the robot can always keep four points of contact with the terrain in a passively, self-adapted fashion.

After experimenting with a prototype made with resin and low-infill 3D printing, the team decided to invest on a definitive model for the wheels, based on aluminum and rubber. A CNC machine toolpath with multiple tools was created to replicate more durable and lightweight wheels easily, and support surrounding rubber tires with much higher across all common surfaces.

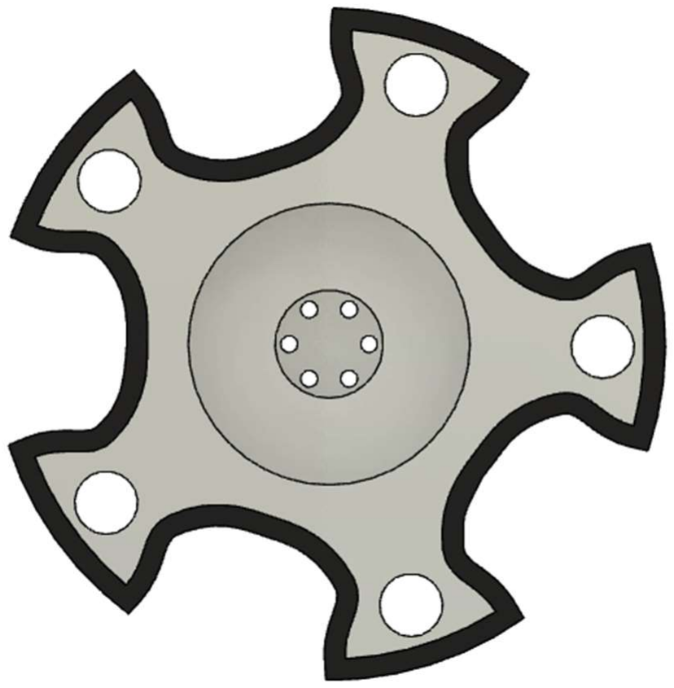
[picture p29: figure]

12

Arm

The arm is used to manipulate objects during mobile operation. It has to be able to rotate, extract, precisely touch and allow inspection of relevant features in the environment, that can be positioned in a variety of ways. Therefore, a movable arm was designed from the ground-up to attend those tasks.

Driven by four MG996R and two MG90S servo motors, the arm does not increase the size of the robot (height excluded) when retracted and can reach forward up to two times the chassis length when fully extended. Furthermore, the position of all joints can be controlled independently and precisely.

The end claw has a large, wavy area of contact that can easily attach to objects such as pipe caps. Thanks to two small arc-shaped pieces attached to each finger, it can open and close in a translation-only direction of movement, instead of rotating like human fingers. This is advantageous because the claw can always keep a larger area of contact with the object and evenly distribute the imposing weight.

Electronics

For the electronics, we started the project with the goal to build our own PCB, and with it, avoid some problems of using cables, bad contacts and all the things that made you crazy at the competition due using cables.

Motor Drivers

Everyone when get in the robot’s world use the h-bride L298n, super simple to program. However, this h-bride is not efficient energetically, it doesn’t use CMOS technology, and due that have a considerable loss of energy.

To solution this problem we are using another h-bride, a super version from L298n, but using CMOS technology, the VNH2SP30 Dual Driver. This driver can control 2 motors DC, with 30A of current.

13

We decided to use 4 motors, one at each wheel, so we are using 2 h-bridges to control all of them.

Our version is a shield to Arduino uno’s, as the image above. This motor drive uses the following ports to control the motors:

- Digital 4: InputB from motor 1
- Digital 5: PWM from motor 1
- Digital 6: PWM from motor 2
- Digital 7: InputA from motor 1
- Digital 8: InputA from motor 2
- Digital 9: InputB from motor 2
- Analogic 0: Enable from motor 1
- Analogic 1: Enable from motor 2

The logic from VNH2SP30 is the same as L298n, the only difference is the enable pins, with need to be HIGH to work.

Voltage Regulator

Our arm works with servo motors, and they are 6 volts. We would need another battery to make the arm work, instead of that we are using a voltage regulator. When we read it under internet, we imagine a 7806 (a simple voltage regulator to 6V).

14

But previously, we talked about energy efficiency, we this CI is not so efficient, actually, depended on the current, we can have a efficient less 50 %, that would imply a lower life from battery.

To avoid it, we choose the following component, the LM2576.

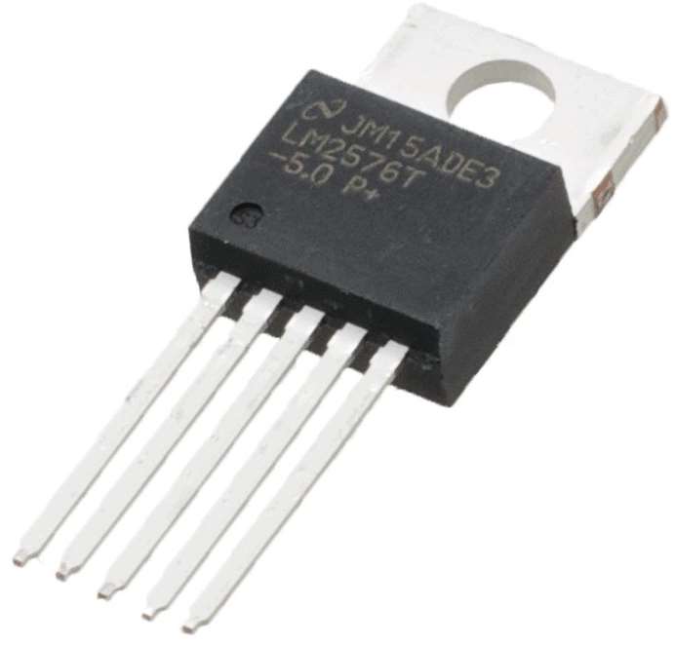
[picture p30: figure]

This component is a regulated voltage tensor, with a higher efficiency. We used the circuit indicated from the fabricant, at DATASHEET.

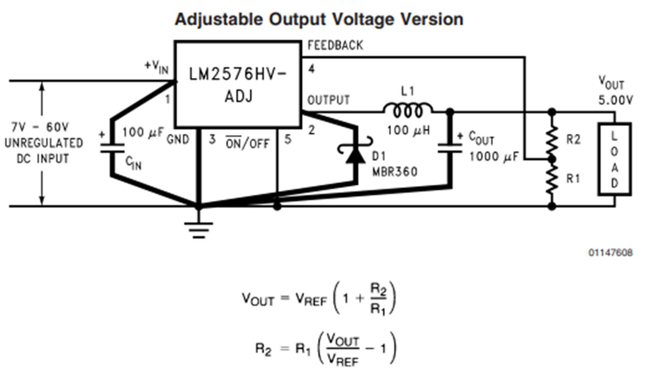
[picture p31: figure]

View the datasheet at:
https://datasheetspdf.com/pdffile/61720/NationalSemiconductor/LM2576/1

15

PCB

To combine everything and make it simpler to use we projected the PCB to receive the Arduino mega, the voltage regulator circuit, the inputs from the servos, the inputs from CO2 sensor and the thermal camera input.

For project it, we used the software Proteus, with our college gave us the license. Our schematic follows bellow:

In the schematic we can verify 5 regions, two represent the h-bridges, one represents servos inputs and the battery input, the other the Arduino mega input with the sensor and thermal camera and the last, the voltage regulated circuit.

On our first version we had space problems, so we decided to take out the inputs that we were not using from Arduino mega. This way, we got more space to make the lines on board. Also, on the first version, we had a problem with the space to put the inductor and the capacitor from 1000 μF. For simplify it, we put a T-block connection and the problem to put the component was solved. So, we had the following result to the board:

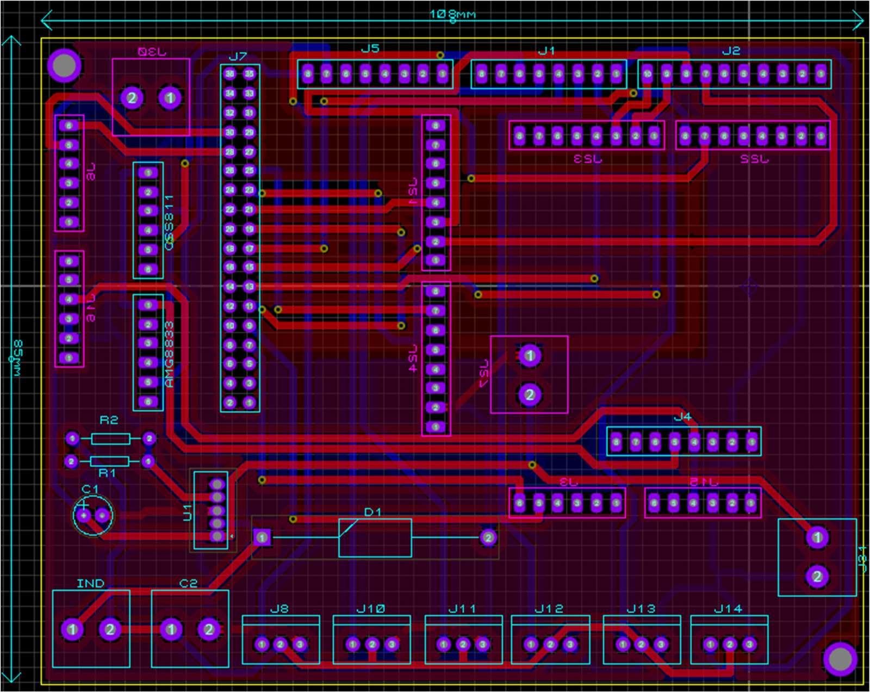
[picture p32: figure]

16

To attach on the robot, we put two holes to attach using screw. The board is 2 faced, in another word, it conducts in both sides, the red part conduct at the top, and the blue part conduct at the bottom.

After finished we had the following result:

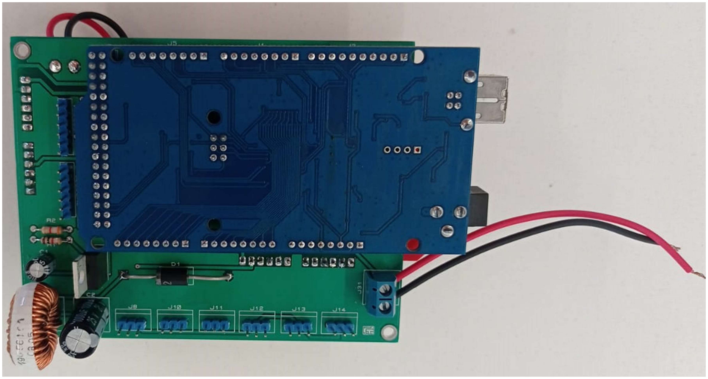
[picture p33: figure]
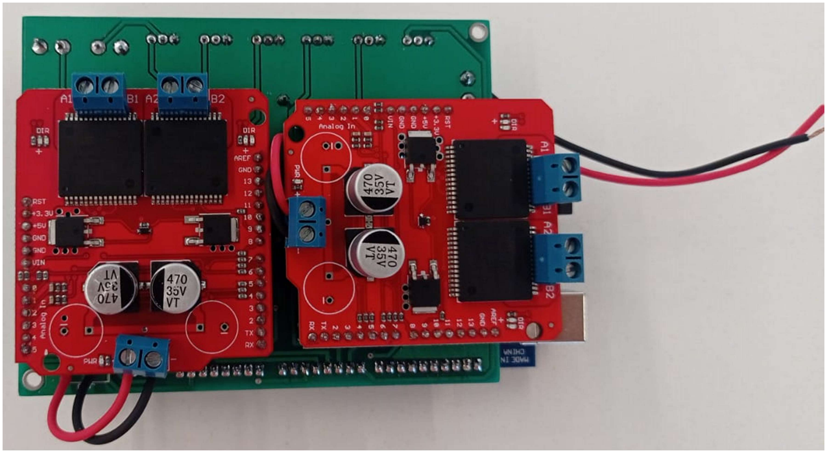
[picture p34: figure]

All the inputs from PCB have cables, specially done, for make this connection. On the photos we can see red and black cables. On the board are the cables that support the power of the h-bridges. The other one was to test the boar but are going to receive the battery supply. All the files to make the board can be find at the team github, also you can check pdf from the schematic, bottom, and upper face from the board.

17

We haven’t mentioned the Jetson Nano yet, but it is used to supply the Arduino, using the serial port. This way, the Arduino is supporting the power for the thermal camera and the CO2 sensor. Besides that, the power bank is responsible to supply the Jetson Nano, this way, we have the control and power parts with different sources.

Communication

The robot uses two forms for communication, one is for be the bridge between the notebook and the jetson nano, and the last one is used intergrade all the sensor, Arduino with the Jetson Nano.

VNC

VNC (Virtual Network Computing) is an internet protocol that allows viewing of remote graphical interfaces over a secure connection. In another words, we are going to access Jetson Nano using it, with an ethernet cable.

Download at: https://www.realvnc.com/pt/connect/download/viewer/

For this communication, we are using a switch, as the image.

The switch can send and receive data if we use the cable directly on Jetson it would not be possible. At this point, we can access all graphic interface from Jetson only using this switch and an ethernet cable, ready to start the set up and configurations.

18

ROS

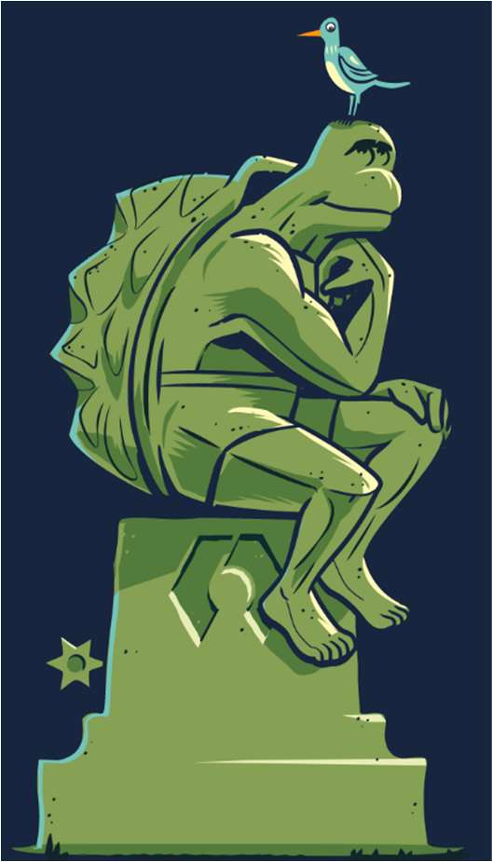
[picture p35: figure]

ROS (Robot Operating System) is a tool to make easier and simple the communication between the robot and all the peripherals. Each peripheral can be imagined as a node, and this node something only read, sometimes only write, or can do both. The node can be a sensor, a motor, an Arduino, anything you need, and it is open source. Now more at: https://www.ros.org .

For our robot we are using ROS to make Arduino and jetson communication, everything that is connected on Arduino are receiving order from Jetson and completing their tasks using ROS. Jetson is our central part of communication and responsible from all the actions, read sensor, turn on the motors, everything using ROS. The next lines will clarify how we did it and give you move details how do the same.

Software Overview

Running software on the robot is divided in 3 parts that operate asynchronously. C++ is utilized for the main code, which is responsible for user interfacing and machine vision algorithms, utilizing OpenCV, as well as communicating with the Arduino via ROS-Serial.

The Arduino board´s code is responsible for low-level interfacing of motors, thermal sensor, and gas sensor with PWM and I2C communication protocols. This is

19

uploaded to the board via the Arduino IDE installed on the main board. Lastly, a set of Python scripts is used to launch base ROS nodes and handling input from the Lidar and Realsense sensors. These are manifested by the laser_scan and odometry-related topics respectively.

The team used Visual Studio Community, Visual Studio Code and Sublime Text 3 during the developed of all self-made scripts used by the robot.

Setup

To evaluate and run the software, a few dependencies have to be present on the target environment. The team recommends the utilization of Ubuntu 18.04LTS as the operating system for all steps.

Firstly, the user is required to install ROS on their machine. More instructions on this task can be found at http://wiki.ros.org/ROS/Installation (for Ubuntu 18.04, the Melodic Morenia distribution is recommended). This is the middleware required for all virtual nodes to communicate.

Additionally, OpenCV, ZBar and SDL are required for the main portion of the software to execute correctly. To do so, run the following commands at root level:

git clone https://github.com/libsdl-org/SDL
cd SDL
mkdir build
cd build
../configure
make
sudo make install

cd ~

sudo apt update

sudo apt-get install libzbar-dev

sudo apt install -y cmake g++ wget unzip

20

wget -O opencv.zip
https://github.com/opencv/opencv/archive/4.x.zip

unzip opencv.zip

mkdir -p build && cd build

cmake ../opencv-4.x

cmake --build .

Arduino IDE should be installed to manage and upload code to the Arduino Mega. Instructions to do this on Linux machines can be found at https://docs.arduino.cc/software/ide-v1/tutorials/Linux. Lastly for dependencies, the user can install SoX to transmit input from the robot´s microphone to the operator in real time. This can be done via the command:

sudo apt install sox

To run the team´s code, use git to clone the repository at https://github.com/InsperDynamics/REDOX-RoboCup-RMRC-Challenge.

The Arduino_Side folder contains software to be uploaded via ArduinoIDE, and the main C++ software is found at Machine Vision and should be compiled via g++. Use catkin_make command to build necessary ROS packages prior to launching the interface.

To access the robot via VNC, the team recommends the usage of VNC Viewer. The instructions on this page can be used to find the IP address of the main board: https://help.ubuntu.com/stable/ubuntu-help/net-findip.html.en. In case of difficulties while trying to forward input from the gamepad to the VNC server, the user can use USB/IP (install and setup instructions at http://usbip.sourceforge.net/ ).

21

Jetson Nano

The Nvidia Jetson Nano 4gb Developer Kit was chosen to be used as the main processing unit of the robot, and is responsible for communicating with the Arduino, high-level sensors, and operator machine, as well as running the machine vision algorithms and organizing autonomous movement.

Designed for machine learning and dynamic robotics in mind, it contains a 128-core NVIDIA Maxwell™ architecture-based GPU, a Quad-core ARM CPU, 4gb of LPDDR4 RAM and has support for Linux for Tegra. All on a compact (100mm x 80mm) and affordable package. It also contains 4 USB-3 ports, gigabit ethernet, a CSI port and GPIO. This makes it very suitable for running all necessary processes required for operation in parallel, while being powered with 5V via micro-USB.

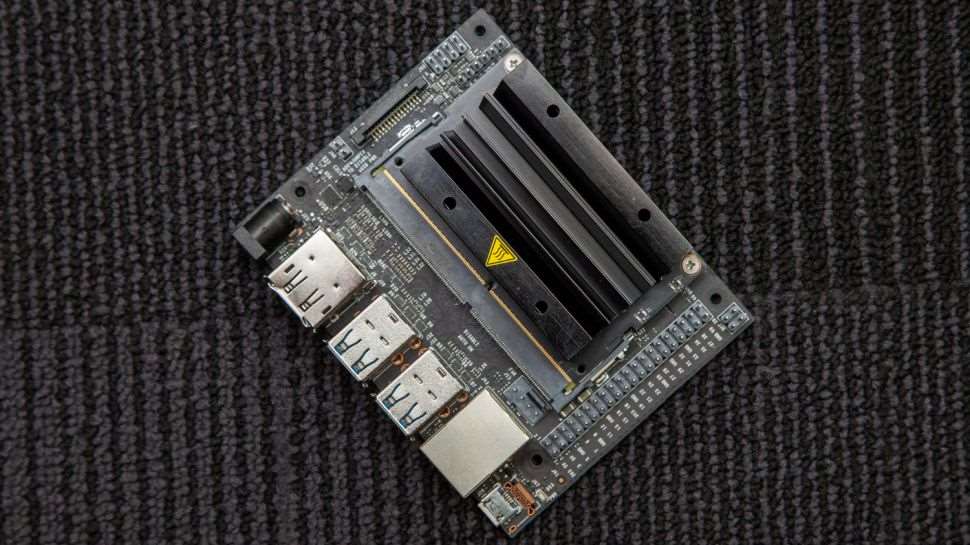
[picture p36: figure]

Sensors

The competition has two specific task that need an external sensor, one is to show a thermal image from the place and the other is to show the concentration of CO2.

Their connections with the Arduino can be checked at the schematic from PCB, some explanations will be given on the next lines. Also, is important say that both only use 4 pins to work, as showed at schematic, 2 for supply and 2 for communication.

22

Thermal Camera

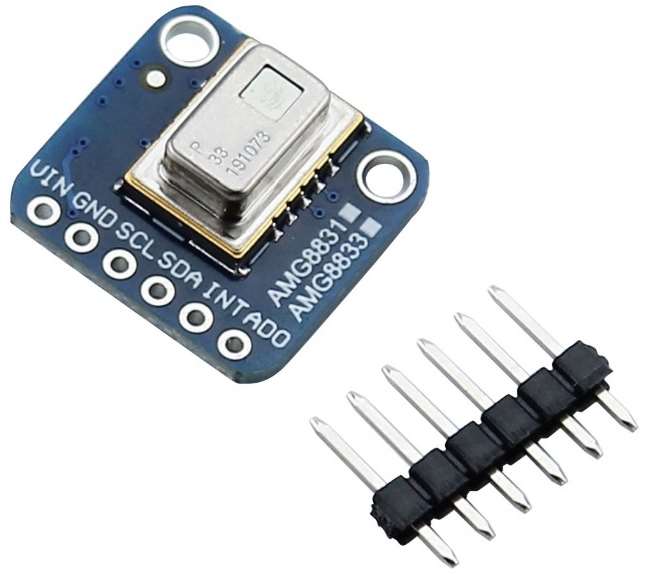
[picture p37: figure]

The thermal camera which we are using is the AMG8831, that has support for Arduino, raspberry and other with I2C communication. This electronic module has and high efficiency and is based on Infrared heat detection sensor that allows the user to detect movement in dark environments, for example.

This sensor has a matrix of 8x8 thermal sensors, and returns a matrix of 64 temperature individual reading, and has a work like a professional thermal camera.

It can identify temperature between 0ºC to 80ºC, also has and precision of ± 2,5 ℃. This module works with 3,3 V, that comes from Arduino, and is connected on SDA and SCL pins from Arduino mega. This sensor represents a node from ROS, making everything more simple and easier to organize on coding.

Know more at: https://learn.adafruit.com/adafruit-amg8833-8x8-thermal-camera-sensor .

23

CO2

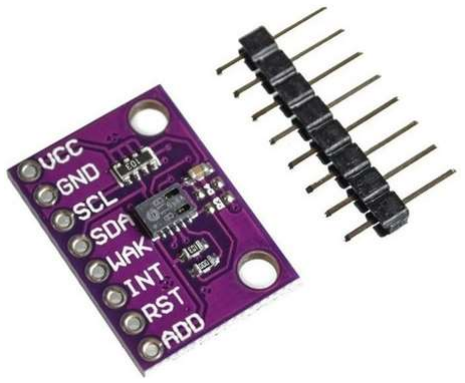
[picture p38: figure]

The CCS811 is a low power miniature digital gas sensor for monitoring air quality. A metal oxide sensor is integrated to measure the total volatile organic compounds equivalent of TVOCs, making it possible to monitor air quality when working in conjunction with microcontrollers, only requiring I2C serial communication.

The module is based on unique microplate technology, meaning the plate presents a highly reliable solution for projects that require gas sensor, fast cycle times and a significant reduction in average power consumption. The integrated MCU manages the sensor trigger modes and the measured data.

The CCS811 supports intelligent algorithms to process measurements and output an equivalent TVOC value, as well as supporting multiple measurement modes that are optimized for low power consumption, thus extending battery life in portable devices.

He also requires 3,3 V of power and comes from Arduino. His pins from CLOCK and DATA (SCL and SDA) are connected in series with the same pins from the thermal camera, and them connected on Arduino’s I2C pins.

Learn more at: https://www.sparkfun.com/products/14193 .

24

Lidar

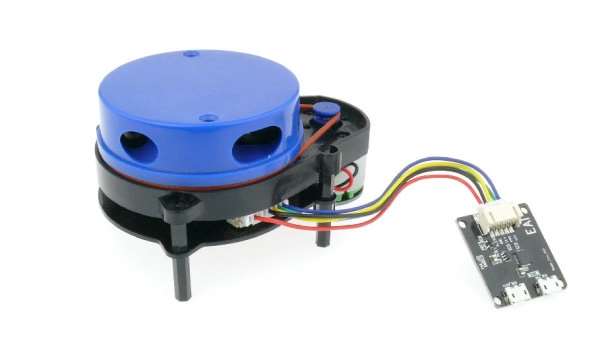
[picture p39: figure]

Autonomous mapping is achieved using a compact rotating laser distance sensor module, mounted on top of the chassis. This is very useful not only for autonomous movement planning, but also for localizing the robot in relation to features present in the map without getting lost. The YDLidar X4 is a low-cost solution for measuring distances of 12 centimeters up to 10 meters, in two dimensions.

Lidar stands for light detection and ranging and uses pulsed laser light to measure the distance to an object. The laser is reflected off the surface of the object, and the distance to the object is determined by measuring the time it takes for the light to reach the sensor. Typically, lasers are chosen that use wavelengths of light outside the visible spectrum, usually infrared.

Power is supplied directly to the module via USB, and a second port is connected to the power bank present on the robot for the event of power supply insufficiency.

Since official drivers and ROS package support exists, interfacing with the lidar is a rather simple task. It is worth noting, however, that in the case of our robot, the module is placed upside down to avoid making the scan plane sit above the top plane of the arena walls when traversing large obstacles. Because of this, an inverted transform data is used for accurate scanning in the software.

25

Realsense T265

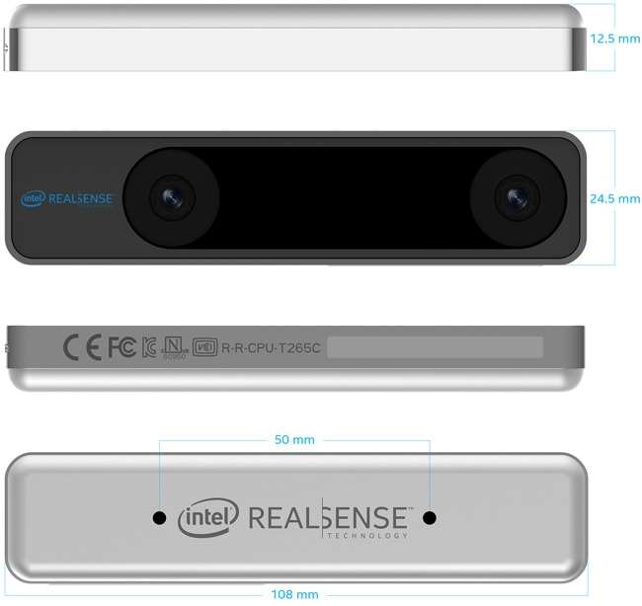
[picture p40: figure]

For the front camera of the robot, an Intel Realsense T265 tracking camera was used. This module combines two OV9282 imagers with fisheye lenses, a BMI055 IMU and an Intel® Movidius™ Myriad™ 2.0 visual processing unit to deliver Visual Inertial Odometry.

Designed to work both indoors and outdoors, the camera can automatically triangulate visual features in the environment to obtain positional information that gets published to our ROS ecosystem. It helps to mitigate drift generated from Lidar-only SLAM and increase mapping confidence, even if the robot is suddenly transported from one part of the arena to another.

The wide FOV also benefits teleoperation and human control. With 163 degrees globally, the operator can have a better understanding on what is in front, above, below or on the sides the robot while moving quickly, securing pose data at the same time. By applying an anti-distortion algorithm, it also provides enough image resolution for detection of far away objects.

26

The only encountered downside by the team is the fact that this camera can only output images in grayscale. For color recognition, other cameras present on the robot should be used instead.

Other Cameras

Along with the Realsense unit, the robot contains a back camera and a claw camera. Both can output colored images at 1080p resolution.

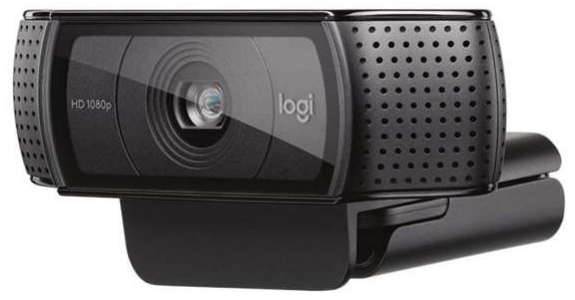
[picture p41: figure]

On the back, a Logitech C920 webcam is used to transmit video feed when operating in backwards motion. This is very helpful in scenarios where the robot reaches a dead-end and must return, preferably without having to turn around its own axis, something that happens constantly in RMRC. It was chosen due to its high resolution at 30 frames per second, ability to automatically adjust focus, contrast and saturation (this is achieved by RightLight 2 technology), and good FOV (78 degrees horizontally).

The C920 is also used for the audio input of the robot thanks to the two omnidirectional microphones connected to the same port of its imager.

27

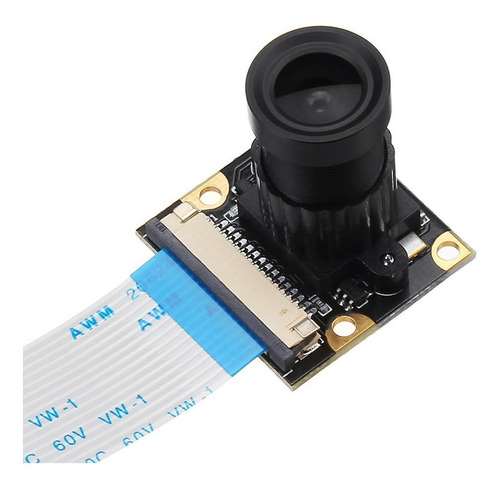
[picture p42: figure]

For arm operation/inspection, an Ov5647 is attached to a support sitting above the robot´s claw. It is a small camera with 60 degrees of horizontal FOV, that takes advantage of the CSI camera port present on the left side of the Jetson Nano.

Object Detection

Regarding object detection, the robot can detect hazmat, QR codes and motion.

To implement hazmat detection, we firstly tried to create our own model. With this objective, we gathered a dataset composed of 14 categories and started to annotate the images with Pascal-VOC to train a Yolo V4 based model. Unfortunately, we had a setback; our hardware was not good enough to train a proper model and our time was short to manually annotate the 2000+ images.

In the meantime, we found Mobile Robotics Laboratory’s YOLO V3-tiny, based model, DeepHAZMAT, as a replacement for our model. This open-source model was thoroughly crafted using real life hazmat signs, photographed form multiple angles. OpenCV, a computer vision library, reads both weight and configuration files of the model, constantly checking the input image for potential hazmat and keeping score of their confidence levels. This model’s dataset is made of 13 labels, detailed hereafter:

28

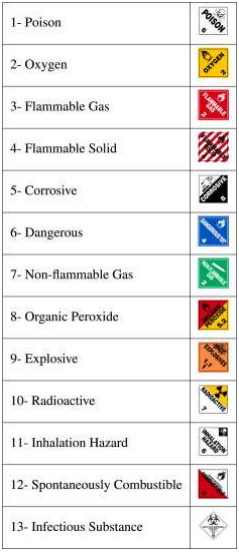
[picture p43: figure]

Additionally, a non- maximum suppression algorithm filters the best candidates of the frame, as the areas surrounding hazmats tend to trigger the model with a lower score.

Motion detection is achieved via frame difference extraction. Each new obtained frame is subject to a Gaussian blur filter, a frame delta is then calculated, filtered and dilated. OpenCV´s findContours() method is then used to find all highlighted blobs in the delta frame, which get filtered by height-width ratio before being draw on screen.

29

The previously stated approach has proven to be very effective for detecting small, rapidly moving objects, especially high-contrast blobs, hence why we adopted it for RMRC black dot detection.

As for QR code detection, ZBar’s bar code reading C++ library was used to detect QR codes on each frame. Both forms of object detection have visual representation on the interface.

Interface

The graphical user interface utilized by the operator was entirely built in C++, utilizing OpenCV to handle all windows. It is designed for minimum complexity and ease of use since the team opted for a dual-monitor approach. Almost all controls are handled via gamepad, which is autodetected by the program, leaving only what is necessary for operation visible to the operator.

Most of the left monitor area is utilized by the current camera feed, which can be switched via the L/R buttons on the gamepad. On the upper left corner, the thermal camera feed is formed in real time, with each pixel ranging from a dark blue tone to red, according to its reading, and then upscaled. Similarly, a large yellow line is formed underneath to indicate the measured level of CO2 concentration in front of the robot.

On the right-hand side, a set of sliders is spawned for control of the arm claw. The position of each servo motor can be directly controlled with a mouse, this allows the operator to use its entire arm to precisely manipulate each joint. In contrast, moving the robot wheels is entirely based on analog joystick output, so that different velocity states can be input quickly.

30

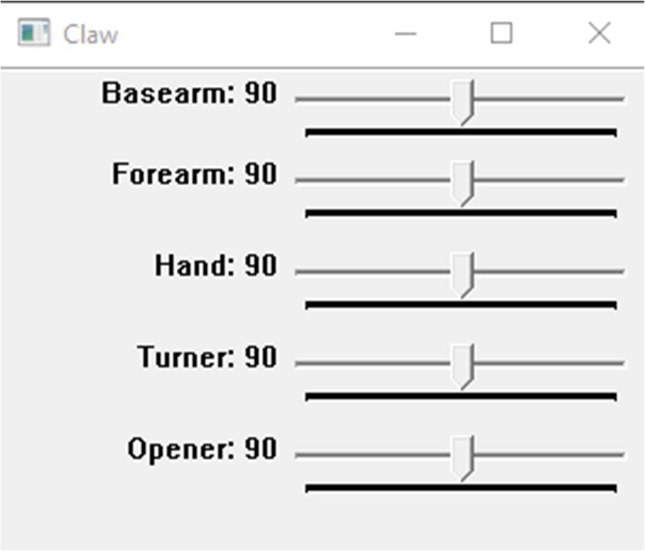
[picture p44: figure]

The other attached monitor should be used to render Rviz or a similar visualization (e.g., Cartographer) program during operation. This is additional feedback regarding estimated states of the robot and can be useful to ensure that the robot is moving properly and mapping the environment as intended, as well as calculated trajectory, for autonomous operation. A single button on the gamepad is used to alternate between manual and autonomous control, and another for turning image post-processing on or off.

Autonomous Part

An autonomous mode is available, which allows the robot to simultaneously map the environment, keep track of its position and control its trajectory. This is achieved using ROS’s gmapping and move_base packages.

Gmapping is a package that runs a simultaneous localization and mapping (SLAM) algorithm. Its only node, slam_gmapping, constantly updates a map (OccupancyGrid) and the robot’s position within it. The requirements of the SLAM algorithm are Lidar’s laser scan input, Realsense’s odometry data and the required tf transformations for both sensors.

As the sensors are placed in different positions of the robot, a reference point must be defined to successfully organize its movement, which is called base link. With this matter in mind, a tf transformation is used to create an offset to the values of a sensor, associating the information to base link. The required transformations are base_link

31

←Scan, which set a base_link point based on lidar’s data, odom ← base_link, which corrects Realsense’s odometry value to base link’s position, and map ← odom, which associates the robot’s position to a fixed reference point of the map.

While slam_gmapping is running, both map’s OccupancyGrid and transformation are constantly updated. From this data a goal pose is calculated, also associated with the map’s fixed reference point, and subscribed by move_base. Afterward, move_base publishes to /cmd_vel the velocity needed to assure that the robot follows the desired trajectory.

Costs

Everything used on the robot is listed on the following table, everything is on the Brazilian coin, on the end we converted it do American Dolar for possible future comparation between the other teams.

Component | Amount | Unitary Cost (BRL) | Total Cost (BRL)
CO2 Sensor: CCS811 | 1 | R$ 80,00 | R$ 80,00
Thermal Camera: AMG8833 | 1 | R$ 240,00 | R$ 240,00
VNH2SP30 Dual Driver | 2 | R$ 130,00 | R$ 260,00
Arduino Mega 2560 | 1 | R$ 140,00 | R$ 140,00
Servo Motor MG996R | 4 | R$ 35,00 | R$ 140,00
Servo Motor MG90S | 2 | R$ 25,00 | R$ 50,00
Nvidea Jetson Nano 4gb Developer Kit | 1 | R$ 1400,00 | R$ 1400,00
Intel Realsense T265 | 1 | R$ 2165,00 | R$ 2165,00
Ethernet Cable (15 m) | 1 | R$ 30,00 | R$ 30,00
Camera Ov5647 1080p | 1 | R$ 130,00 | R$ 130,00
70:1 Metal Gearmotor 37Dx54L mm 12V (Helical Pinion) | 4 | R$ 155,00 | R$ 620,00
Camera Logitech C920 | 1 | R$ 370,00 | R$ 370,00

32

YDlidar X4 | 1 | R$ 1200,00 | R$ 1200,00
PowerBank 20.000 mAh | 1 | R$ 115,00 | R$ 115,00
PLA Filament (500 g) | 2 | R$ 85,00 | R$ 170,00
Dualsky Eco S 12V 2200mAh LiPo battery | 1 | R$ 115,00 | R$ 115,00
Dual faced Custom PCB | 1 | R$ 430,00 | R$ 430,00
Bearing 6201 Ddu C3 12x32x10 | 1 | R$ 20,00 | R$ 20,00
Xbox 360 Controller | 1 | R$ 60,00 | R$ 60,00
TP-Link LS1005G LiteWave | 1 | R$ 105,00 | R$ 105,00

Total Cost are R$ 7840,00, in American dollar is $ 1.662,50. Note, the conversion between the coins were made in April, so it can change when you are reading this paper.

### Prototype Photos

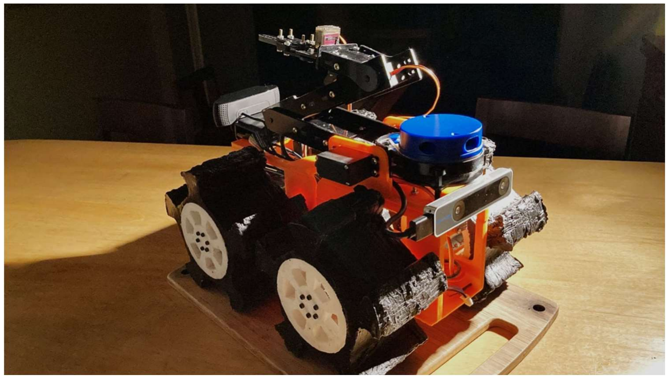
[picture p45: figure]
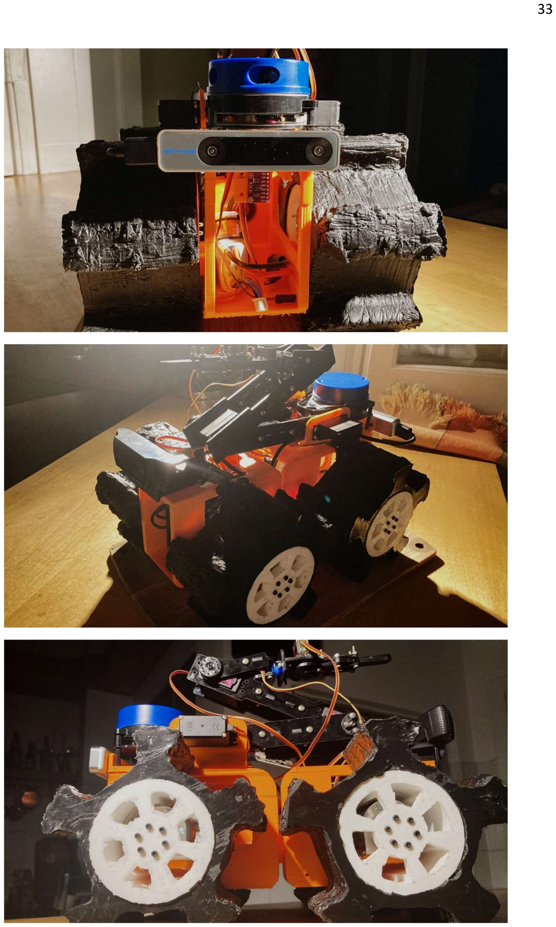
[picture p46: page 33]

33

34

### Future Upgrades

Although the team was satisfied with the overall design of the robot for this edition, a few improvements could be made. These aim to obtain maximum efficiency while keeping its principles, to better attend both the general needs for real rescue scenarios, as well as more specific tasks of RoboCup Rescue.

Firstly, the project could greatly benefit from wireless connectivity. By utilizing a high-range antenna attached to the main board, the necessity of a cable manager on the operation site would be eliminated. This not only reduces human injury risks, but also removes the constraint of the ethernet cable itself, which can tangle, twist or even break depending on the environment.

High-level machine vision and ROS algorithm processing can also be shifted to the operator´s computer. This way, the robot could be redesigned to only comport sensors and lower-level components that we can design, without the need for an onboard GPU for example. The result would be a permission to reduce weight and size of the robot, as well as keeping the high-level source code on a PC for easier access and security.

The arm could also be improved with the utilization of servo units that benefit from daisy-chain technology. Models such as the DRS - 0101 HerkuleX Smart Servo can connect to one another reducing the total amount of wiring on the robot, as well as offering trapezoidal velocity profile, PID and other useful algorithms for precise control applied automatically.

Finally, the team recognizes that higher-resolution thermal imaging sensors and 3D scanning capabilities are more well-suited for real rescue scenarios. Unfortunately, no alternatives that would not significantly increase the cost of the robot were found by the team yet.

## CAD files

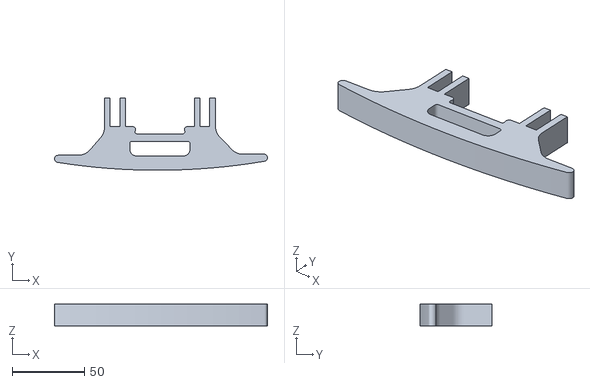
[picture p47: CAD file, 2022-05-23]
3D Models/Bumper.stl
147.8 x 50.3 x 15.0

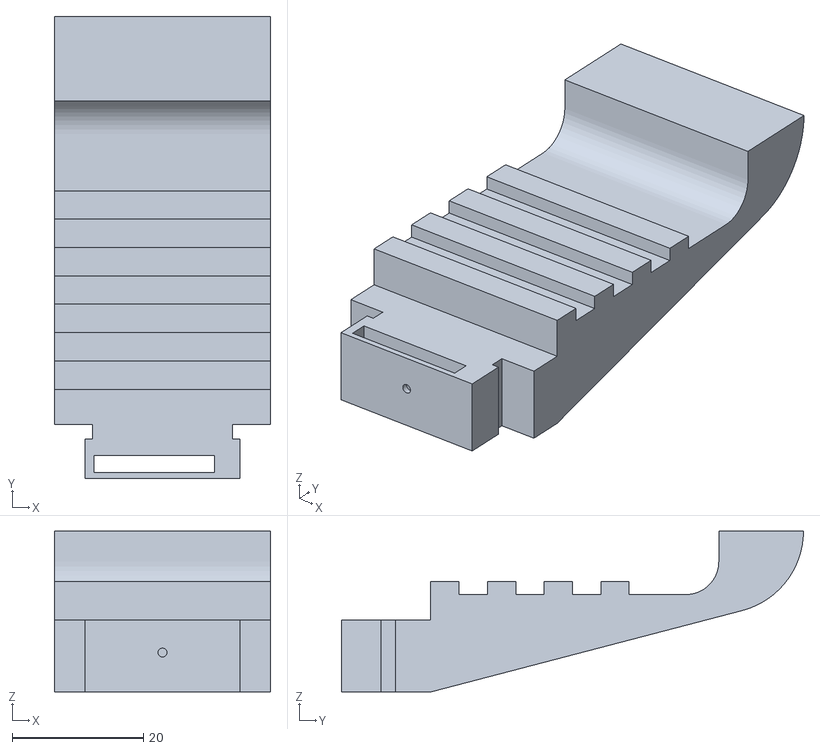
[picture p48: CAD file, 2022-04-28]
3D Models/garra nova/FingerBase_02.stl
32.9 x 70.4 x 24.5

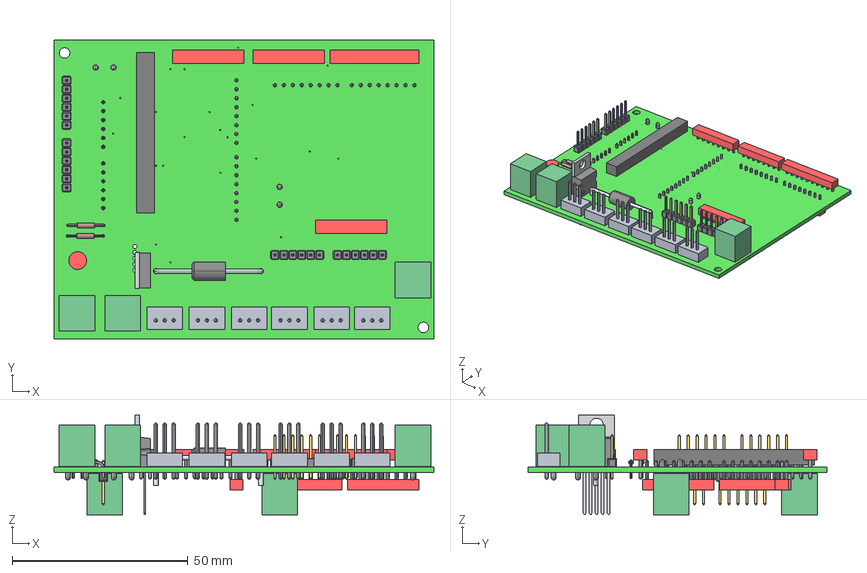
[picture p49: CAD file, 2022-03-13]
PCB/rmrv_v9.STEP
108.0 x 85.0 x 28.3 mm
Layer_1
Pin_1 x 23
Pin_2 x 23
Pin_3 x 15
BODY-TO-220
LEAD-TO220 x 5
HEATSINK-TO-220
=>[0:1:1:2]
=>[0:1:1:3]
=>[0:1:1:4]
EDGE x 42
=>[0:1:1:12] x 6
=>[0:1:1:13] x 6
=>[0:1:1:14] x 6
=>[0:1:1:15] x 6
=>[0:1:1:16] x 6
=>[0:1:1:17] x 6
=>[0:1:1:19] x 6
=>[0:1:1:20] x 6
=>[0:1:1:21] x 6
=>[0:1:1:22] x 6
=>[0:1:1:23] x 6
=>[0:1:1:24] x 6
Pin_4 x 9
Pin_5 x 9
Pin_6 x 9
Pin_7 x 9
Pin_8 x 9
Pin_9 x 2
Pin_10 x 2
Pin_11
Pin_12
Pin_13
Pin_14
Pin_15
Pin_16
Pin_17
Pin_18
Pin_19
Pin_20
Pin_21
Pin_22
Pin_23
Pin_24
Pin_25
Pin_26
Pin_27
Pin_28
Pin_29
Pin_30
Pin_31
Pin_32
Pin_33
Pin_34
Pin_35
Pin_36

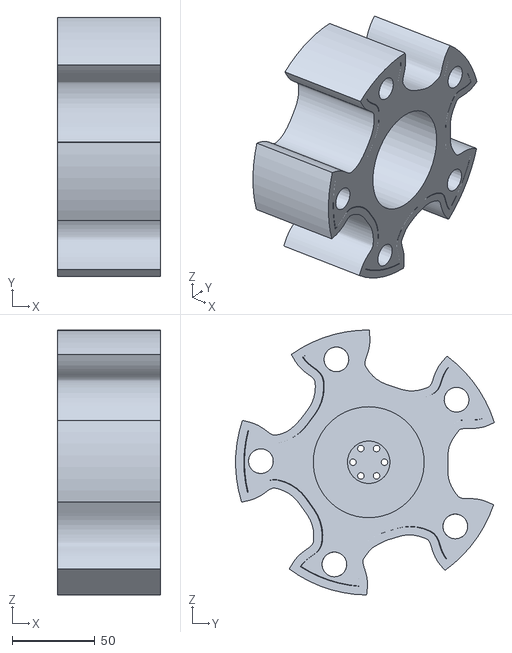
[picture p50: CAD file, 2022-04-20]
ros package/redox_robot_description/meshes/wheel_4.stl
62.1 x 156.2 x 160.0

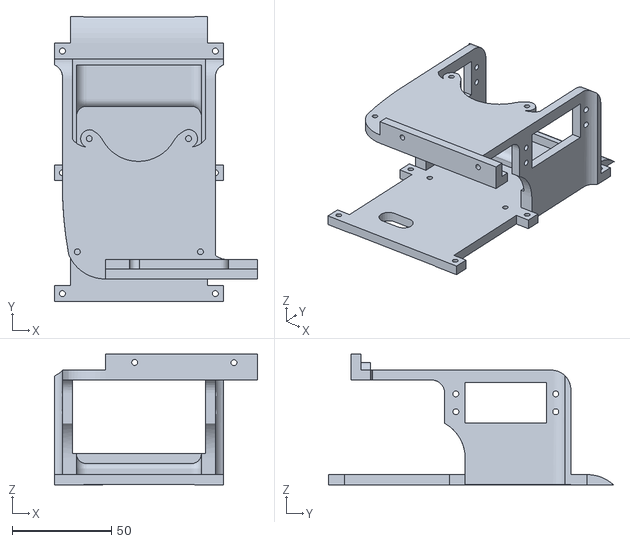
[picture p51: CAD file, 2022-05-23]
3D Models/Body23_21maio (Recortar 2).stl
102.2 x 143.6 x 65.8

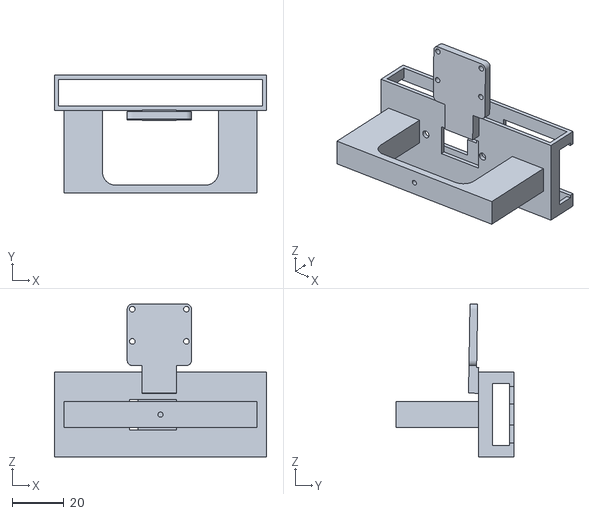
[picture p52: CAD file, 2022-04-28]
3D Models/garra nova/ClawBase.stl
82.3 x 45.7 x 59.4

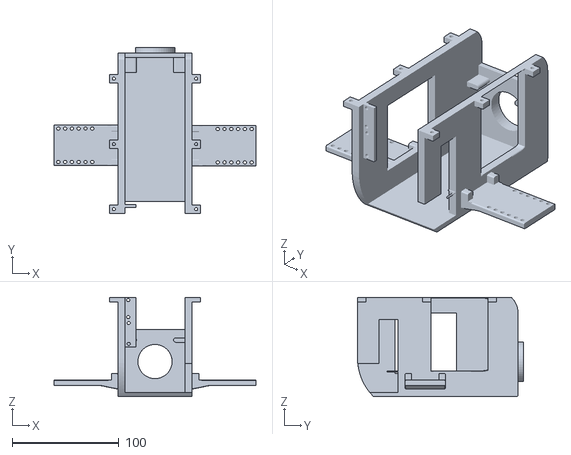
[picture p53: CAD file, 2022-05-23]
3D Models/Body23_21maio (Recortar 1).stl
189.0 x 155.1 x 93.0

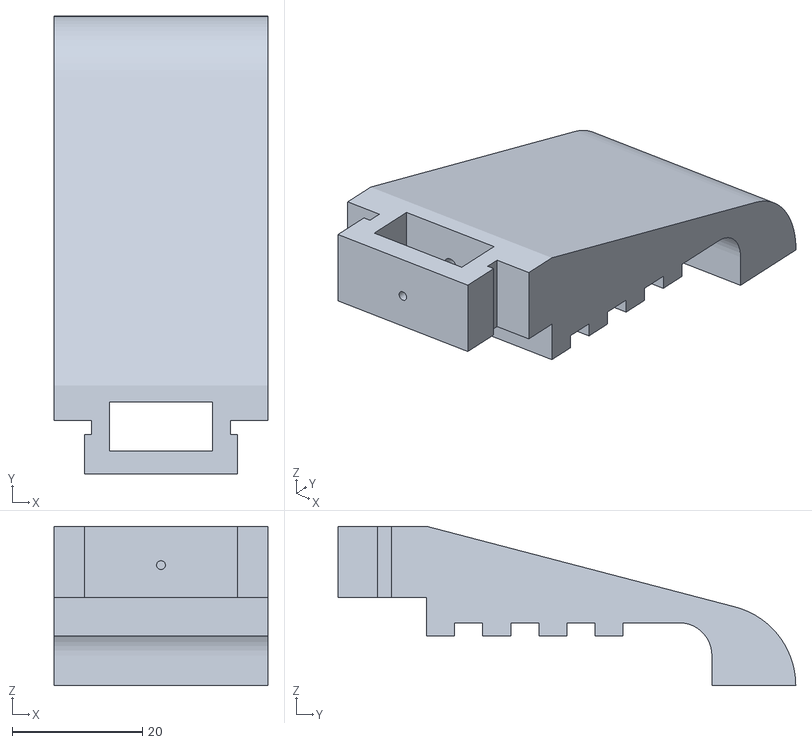
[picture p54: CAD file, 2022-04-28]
3D Models/garra nova/FingerBase_01.stl
32.9 x 70.4 x 24.5

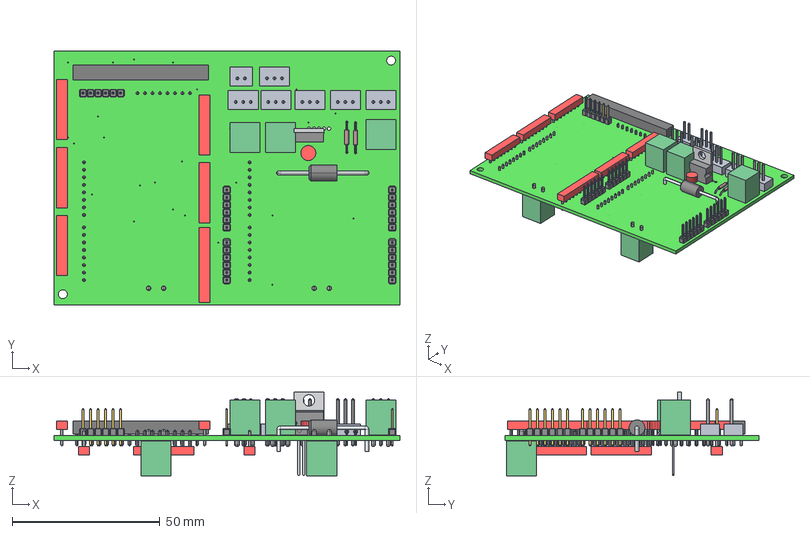
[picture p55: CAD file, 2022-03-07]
PCB/rmrc_v5.STEP
117.0 x 86.0 x 28.3 mm
Layer_1
Pin_1 x 27
Pin_2 x 27
Pin_3 x 18
Pin_4 x 12
Pin_5 x 12
Pin_6 x 12
Pin_7 x 12
Pin_8 x 12
Pin_9 x 2
Pin_10 x 2
Pin_11
Pin_12
Pin_13
Pin_14
Pin_15
Pin_16
Pin_17
Pin_18
Pin_19
Pin_20
Pin_21
Pin_22
Pin_23
Pin_24
Pin_25
Pin_26
Pin_27
Pin_28
Pin_29
Pin_30
Pin_31
Pin_32
Pin_33
Pin_34
Pin_35
Pin_36
BODY-TO-220
LEAD-TO220 x 5
HEATSINK-TO-220
=>[0:1:1:2]
=>[0:1:1:3]
=>[0:1:1:4]
EDGE x 35
=>[0:1:1:12] x 5
=>[0:1:1:13] x 5
=>[0:1:1:14] x 5
=>[0:1:1:15] x 5
=>[0:1:1:16] x 5
=>[0:1:1:17] x 5
=>[0:1:1:19] x 5
=>[0:1:1:20] x 5
=>[0:1:1:21] x 5
=>[0:1:1:22] x 5
=>[0:1:1:23] x 5
=>[0:1:1:24] x 5

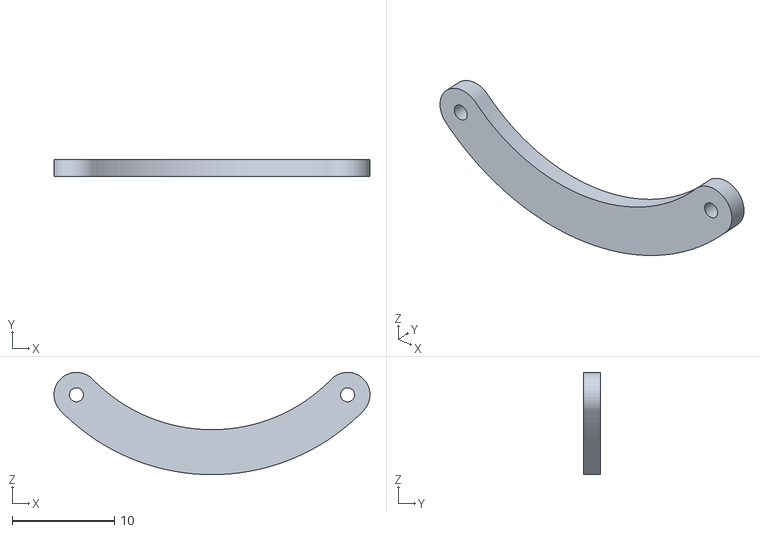
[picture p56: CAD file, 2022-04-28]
3D Models/garra nova/ServoHorn_FingerBase_Connector.stl
30.9 x 1.65 x 9.99

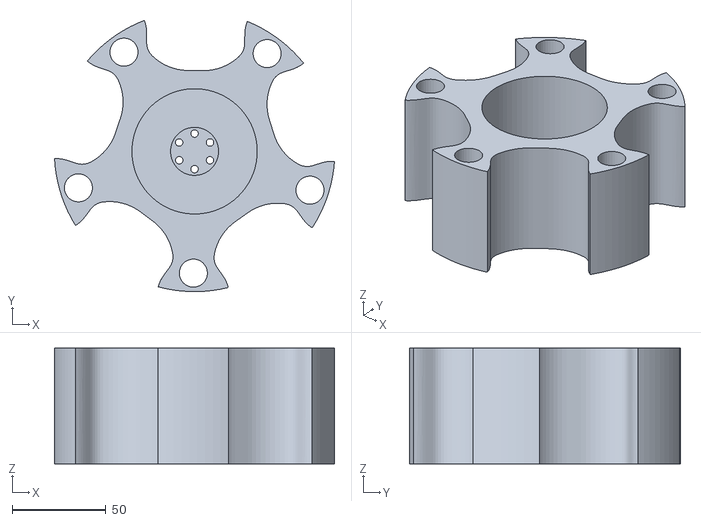
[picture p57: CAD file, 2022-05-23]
3D Models/Roda.stl
149.7 x 145.0 x 62.0

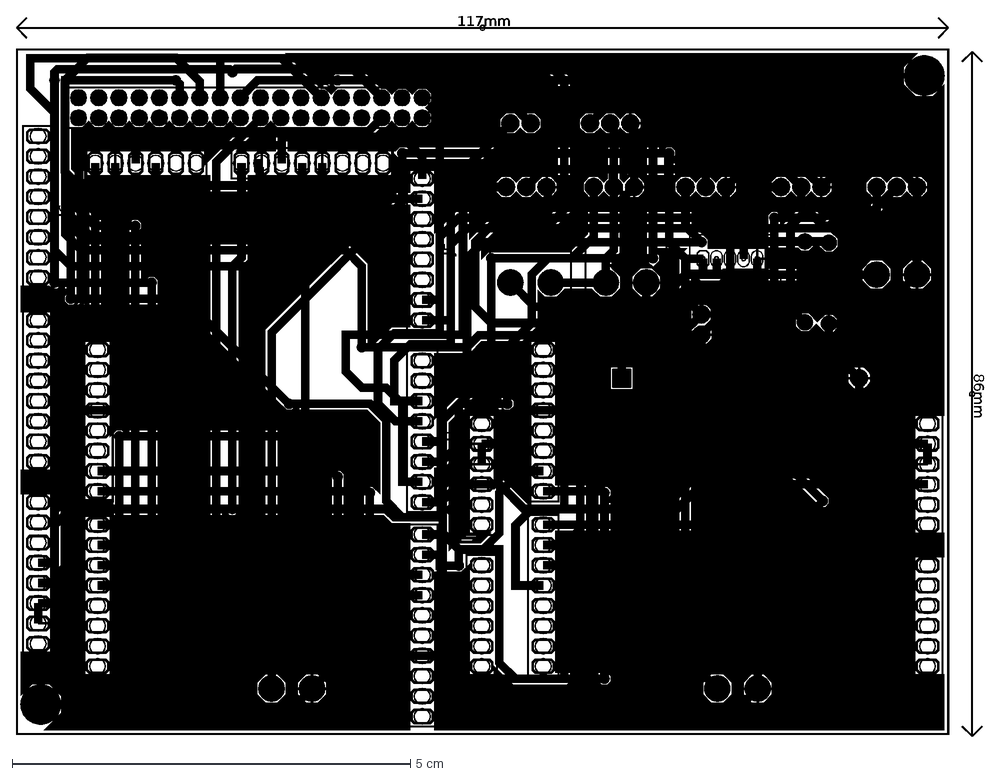
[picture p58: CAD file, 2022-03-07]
PCB/v4_3d.dxf
J7
J6
J3
J4
J5
J1
J2
J31
J8
J10
J11
J12
J13
J14
U1
D1
IND
C1
R1
R2
J9
C2
J18
J21
J24
J16
J30
AMG8833
CSS811
J17
J22
J23
J15
J27
117mm
86mm

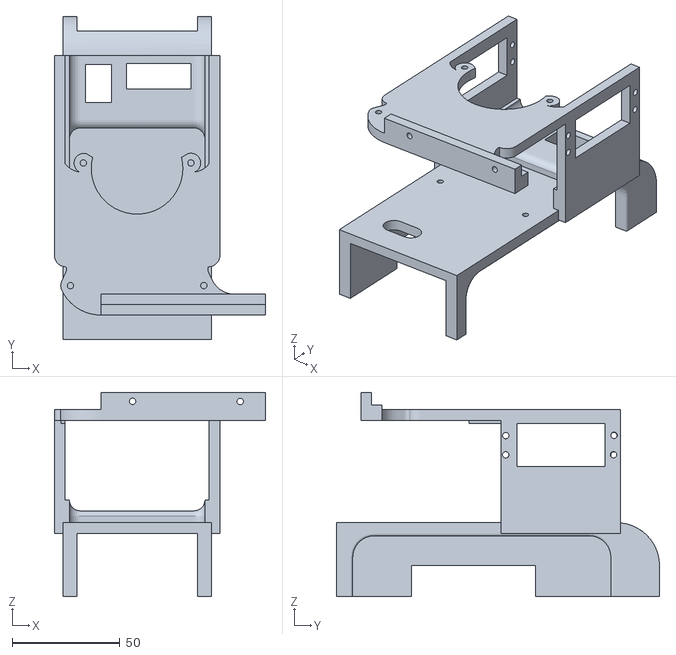
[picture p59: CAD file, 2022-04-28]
3D Models/Body23 (Recortar 2).stl
98.2 x 150.1 x 95.0

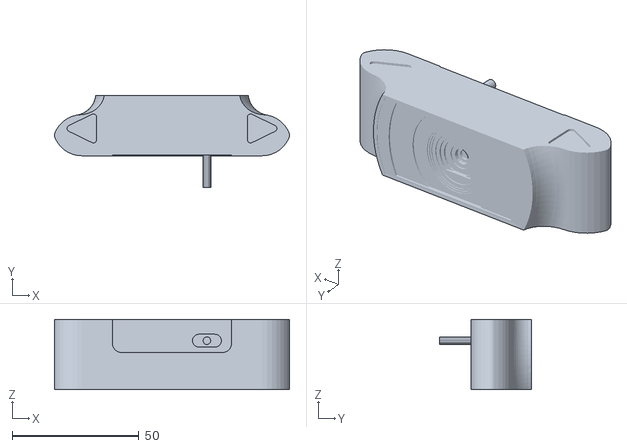
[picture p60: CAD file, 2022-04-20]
ros package/redox_robot_description/meshes/back_camera_1.stl
92.6 x 36.4 x 27.7

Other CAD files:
ros package/redox_robot_description/meshes/wheel_2.stl
ros package/redox_robot_description/meshes/wheel_1.stl
ros package/redox_robot_description/meshes/wheel_3.stl
3D Models/Body1.3mf
3D Models/Body10 (Recortar 1).stl
3D Models/Body10 (Recortar 2).stl
3D Models/Body19 (Recortar 1).stl
3D Models/Pazinha_CONSERTADA.stl
PCB/rmrv_v8.STEP
ros package/redox_robot_description/meshes/base_link.stl
ros package/redox_robot_description/meshes/base_scan_1.stl
ros package/redox_robot_description/meshes/bracket_1.stl
ros package/redox_robot_description/meshes/bracket_2.stl
ros package/redox_robot_description/meshes/bracket_3.stl
ros package/redox_robot_description/meshes/bracket_4.stl
ros package/redox_robot_description/meshes/dcmotor_1.stl
ros package/redox_robot_description/meshes/dcmotor_2.stl
ros package/redox_robot_description/meshes/dcmotor_3.stl
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

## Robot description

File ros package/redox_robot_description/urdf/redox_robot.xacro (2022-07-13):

<?xml version="1.0" ?>
<robot name="redox_robot" xmlns:xacro="http://www.ros.org/wiki/xacro">

<xacro:include filename="$(find redox_robot_description)/urdf/materials.xacro" />
<xacro:include filename="$(find redox_robot_description)/urdf/redox_robot.trans" />
<xacro:include filename="$(find redox_robot_description)/urdf/redox_robot.gazebo" />
<link name="base_link">
  <inertial>
    <origin xyz="0.030018705409207293 0.02277308750672743 0.03005279524109006" rpy="0 0 0"/>
    <mass value="3.8831887887628076"/>
    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
  </inertial>
  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
</link>

<link name="wheel_3">
  <inertial>
    <origin xyz="0.02729659083369923 -0.0003579998502422632 -0.00014058126175340354" rpy="0 0 0"/>
    <mass value="4.750258601717646"/>
    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
  </inertial>
  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
</link>

<link name="wheel_2">
  <inertial>
    <origin xyz="-0.027296318412980913 0.0003572313203910604 -0.00014058126175261598" rpy="0 0 0"/>
    <mass value="4.750258601717646"/>
    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
  </inertial>
  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
</link>

<link name="wheel_4">
  <inertial>
    <origin xyz="0.027296590833699196 -0.00035799985024231873 -0.00014058126175339226" rpy="0 0 0"/>
    <mass value="4.750258601717646"/>
    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
  </inertial>
  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
</link>

<link name="wheel_1">
  <inertial>
    <origin xyz="-0.027296318412980844 0.0003572313203910882 -0.0001405812617526125" rpy="0 0 0"/>
    <mass value="4.750258601717646"/>
    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
  </inertial>
  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
</link>

<link name="gas_sensor_1">
  <inertial>
    <origin xyz="0.004746672182731395 -0.0008000921306509645 -0.007921901743374184" rpy="0 0 0"/>
    <mass value="0.003460388744762866"/>
    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
  </inertial>
  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
</link>

<link name="base_scan_1">
  <inertial>
    <origin xyz="-0.000781 0.088274 -0.123077" rpy="0 0 0"/>
    <mass value="0.0"/>
    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
  </inertial>
  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
    
</link>

<link name="realsense_t265_1">
  <inertial>
    <origin xyz="-0.024754295060534712 -0.006117361074135616 -1.7589246570359762e-07" rpy="0 0 0"/>
    <mass value="0.22482888211310204"/>
    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
  </inertial>
  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
</link>

<link name="hub_4">
  <inertial>
    <origin xyz="0.003113509900325759 -9.136762218298067e-05 -0.00015428718992915869" rpy="0 0 0"/>
    <mass value="0.02001967132782171"/>
    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
  </inertial>
  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
</link>

<link name="hub_1">
  <inertial>
    <origin xyz="-0.003113237479607567 9.059909233208319e-05 -0.00015428718992845179" rpy="0 0 0"/>
    <mass value="0.02001967132782171"/>
    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
  </inertial>
  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
</link>

<link name="hub_2">
  <inertial>
    <origin xyz="-0.00311323747960765 9.059909233206931e-05 -0.00015428718992844398" rpy="0 0 0"/>
    <mass value="0.02001967132782171"/>
    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
  </inertial>
  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
</link>

<link name="hub_3">
  <inertial>
    <origin xyz="0.0031135099003257866 -9.13676221830223e-05 -0.00015428718992917343" rpy="0 0 0"/>
    <mass value="0.02001967132782171"/>
    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
  </inertial>
  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
</link>

<link name="dcmotor_4">
  <inertial>
    <origin xyz="0.02690834299078937 0.007749476584377274 -0.013589835198918437" rpy="0 0 0"/>
    <mass value="0.4471801539290962"/>
    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
  </inertial>
  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
</link>

<link name="dcmotor_1">
  <inertial>
    <origin xyz="-0.02690807057007101 0.007749754885771787 -0.013589835198917991" rpy="0 0 0"/>
    <mass value="0.4471801539290962"/>
    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
  </inertial>
  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
</link>

<link name="dcmotor_2">
  <inertial>
    <origin xyz="-0.026908070570071024 0.007749754885771759 -0.01358983519891798" rpy="0 0 0"/>
    <mass value="0.4471801539290962"/>
    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
  </inertial>
  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
</link>

<link name="dcmotor_3">
  <inertial>
    <origin xyz="0.026908342990789424 0.007749476584377177 -0.013589835198918434" rpy="0 0 0"/>
    <mass value="0.4471801539290962"/>
    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
  </inertial>
  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
</link>

<link name="bracket_1">
  <inertial>
    <origin xyz="-0.002859767439332389 0.015615634272172767 0.006770355606271952" rpy="0 0 0"/>
    <mass value="0.04195982764049011"/>
    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
  </inertial>
  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
</link>

<link name="bracket_2">
  <inertial>
    <origin xyz="-0.0028597674393324307 0.01561563427217276 0.006770355606271971" rpy="0 0 0"/>
    <mass value="0.04195982764049011"/>
    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
  </inertial>
  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
</link>

<link name="bracket_4">
  <inertial>
    <origin xyz="0.002859039860050941 0.015626500151939553 0.006770355606271875" rpy="0 0 0"/>
    <mass value="0.04195982764049011"/>
    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
  </inertial>
  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
</link>

<link name="bracket_3">
  <inertial>
    <origin xyz="0.002859039860050934 0.015626500151939504 0.006770355606271877" rpy="0 0 0"/>
    <mass value="0.04195982764049011"/>
    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
  </inertial>
  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
</link>

<link name="back_camera_1">
  <inertial>
    <origin xyz="2.3451599559846936e-05 -0.0012721615487102378 0.013794968532879703" rpy="0 0 0"/>
    <mass value="0.3938340663114922"/>
    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
  </inertial>
  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
</link>

<link name="thermal_camera_1">
  <inertial>
    <origin xyz="0.009852254547568662 -0.001102102803734406 -0.009785702572175273" rpy="0 0 0"/>
    <mass value="0.004996183093515437"/>
    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
  </inertial>
  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
</link>

<joint name="Rev1" type="continuous">
  <origin xyz="0.0 0.0 0.0" rpy="0 0 0"/>
  <parent link="hub_3"/>
  <child link="wheel_3"/>
  <axis xyz="1.0 -0.0 0.0"/>
</joint>

<joint name="Rev2" type="continuous">
  <origin xyz="0.0 0.0 0.0" rpy="0 0 0"/>
  <parent link="hub_2"/>
  <child link="wheel_2"/>
  <axis xyz="-1.0 -0.0 0.0"/>
</joint>

<joint name="Rev3" type="continuous">
  <origin xyz="0.0 0.0 0.0" rpy="0 0 0"/>
  <parent link="hub_4"/>
  <child link="wheel_4"/>
  <axis xyz="1.0 -0.0 0.0"/>
</joint>

<joint name="Rev4" type="continuous">
  <origin xyz="0.0 0.0 0.0" rpy="0 0 0"/>
  <parent link="hub_1"/>
  <child link="wheel_1"/>
  <axis xyz="-1.0 -0.0 0.0"/>
</joint>

<joint name="Rigid6" type="fixed">
  <origin xyz="0.006734 -0.107777 0.067433" rpy="0 0 0"/>
  <parent link="base_link"/>
  <child link="gas_sensor_1"/>
</joint>

<joint name="Rigid7" type="fixed">
  <origin xyz="0.000781 -0.088274 0.123077" rpy="0 0 0"/>
  <parent link="base_link"/>
  <child link="base_scan_1"/>
</joint>

<joint name="Rigid8" type="fixed">
  <origin xyz="0.079663 -0.101969 0.131791" rpy="0 0 0"/>
  <parent link="base_link"/>
  <child link="realsense_t265_1"/>
</joint>

<joint name="Rigid9" type="fixed">
  <origin xyz="-0.022 0.00775 -0.020424" rpy="0 0 0"/>
  <parent link="dcmotor_4"/>
  <child link="hub_4"/>
</joint>

<joint name="Rigid10" type="fixed">
  <origin xyz="0.022 0.00775 -0.020424" rpy="0 0 0"/>
  <parent link="dcmotor_1"/>
  <child link="hub_1"/>
</joint>

<joint name="Rigid11" type="fixed">
  <origin xyz="0.022 0.00775 -0.020424" rpy="0 0 0"/>
  <parent link="dcmotor_2"/>
  <child link="hub_2"/>
</joint>

<joint name="Rigid12" type="fixed">
  <origin xyz="-0.022 0.00775 -0.020424" rpy="0 0 0"/>
  <parent link="dcmotor_3"/>
  <child link="hub_3"/>
</joint>

<joint name="Rigid13" type="fixed">
  <origin xyz="-0.012688 0.007873 0.034226" rpy="0 0 0"/>
  <parent link="bracket_4"/>
  <child link="dcmotor_4"/>
</joint>

<joint name="Rigid14" type="fixed">
  <origin xyz="0.012687 0.007867 0.034226" rpy="0 0 0"/>
  <parent link="bracket_1"/>
  <child link="dcmotor_1"/>
</joint>

<joint name="Rigid15" type="fixed">
  <origin xyz="0.012687 0.007867 0.034226" rpy="0 0 0"/>
  <parent link="bracket_2"/>
  <child link="dcmotor_2"/>
</joint>

<joint name="Rigid16" type="fixed">
  <origin xyz="-0.012688 0.007873 0.034226" rpy="0 0 0"/>
  <parent link="bracket_3"/>
  <child link="dcmotor_3"/>
</joint>

<joint name="Rigid17" type="fixed">
  <origin xyz="0.109529 -0.065621 -0.007509" rpy="0 0 0"/>
  <parent link="base_link"/>
  <child link="bracket_1"/>
</joint>

<joint name="Rigid18" type="fixed">
  <origin xyz="0.109529 0.095779 -0.007509" rpy="0 0 0"/>
  <parent link="base_link"/>
  <child link="bracket_2"/>
</joint>

<joint name="Rigid19" type="fixed">
  <origin xyz="-0.045966 -0.065213 -0.007509" rpy="0 0 0"/>
  <parent link="base_link"/>
  <child link="bracket_4"/>
</joint>

<joint name="Rigid20" type="fixed">
  <origin xyz="-0.045966 0.096187 -0.007509" rpy="0 0 0"/>
  <parent link="base_link"/>
  <child link="bracket_3"/>
</joint>
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

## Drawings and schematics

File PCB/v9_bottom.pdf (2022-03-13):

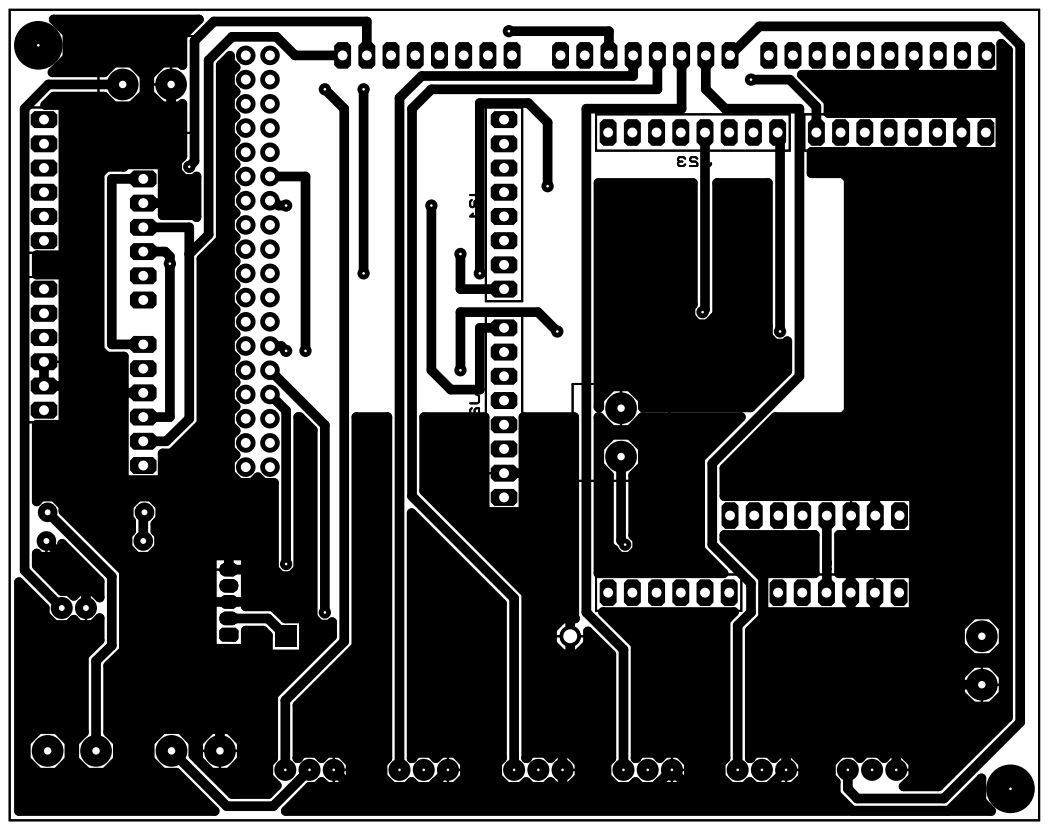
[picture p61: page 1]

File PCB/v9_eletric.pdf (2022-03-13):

J8

J10

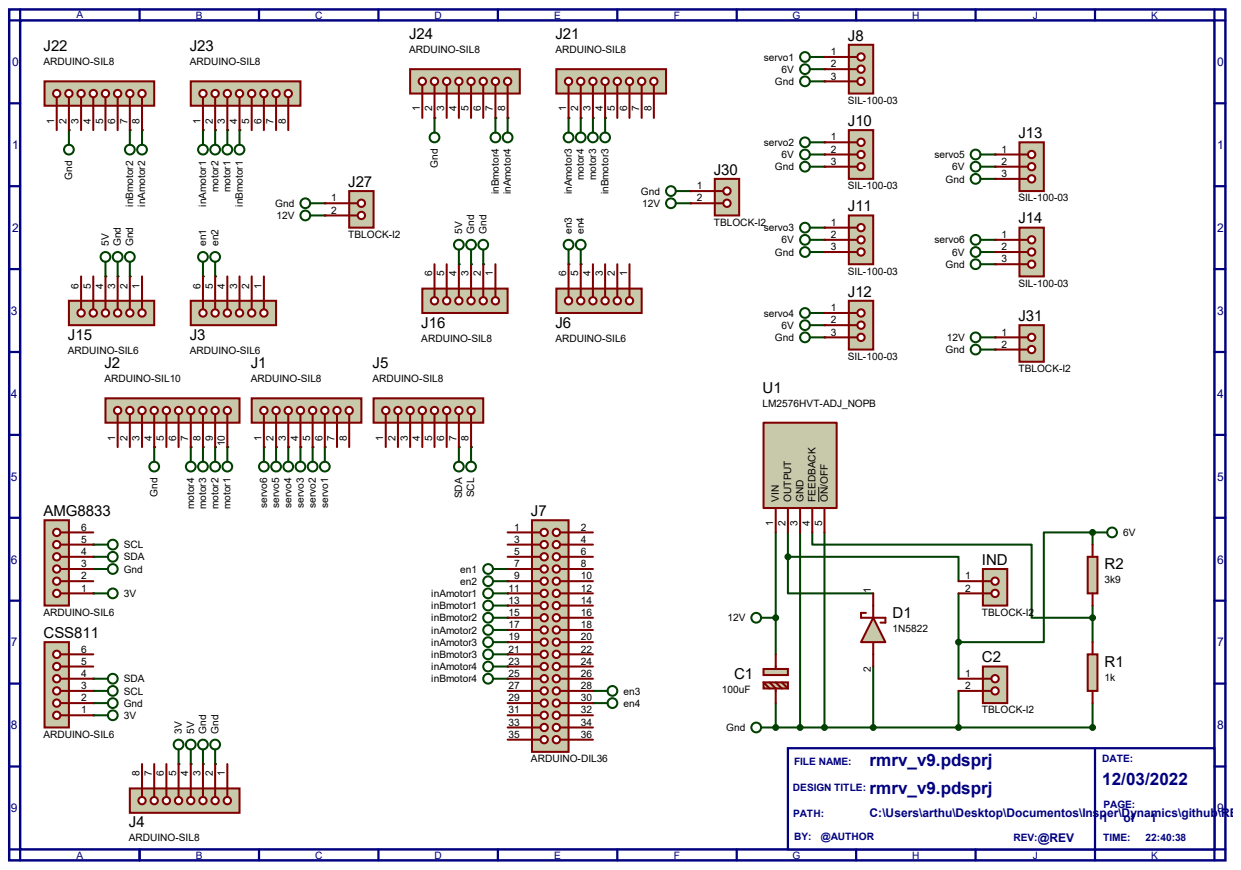
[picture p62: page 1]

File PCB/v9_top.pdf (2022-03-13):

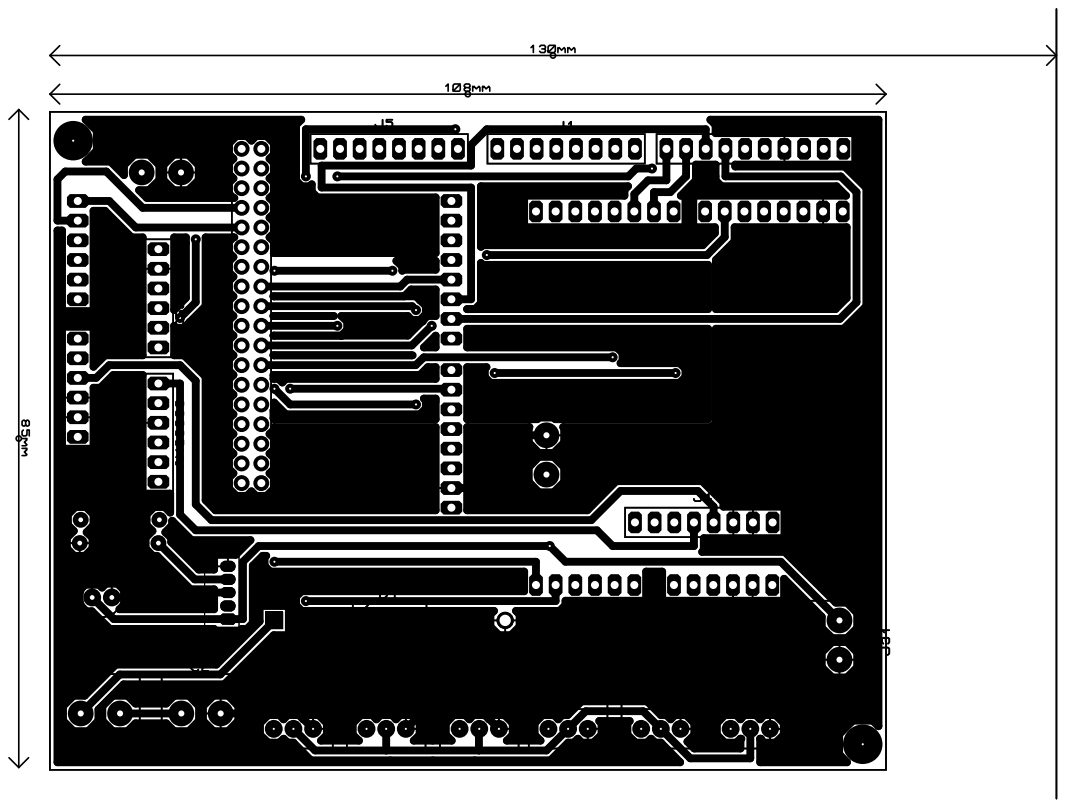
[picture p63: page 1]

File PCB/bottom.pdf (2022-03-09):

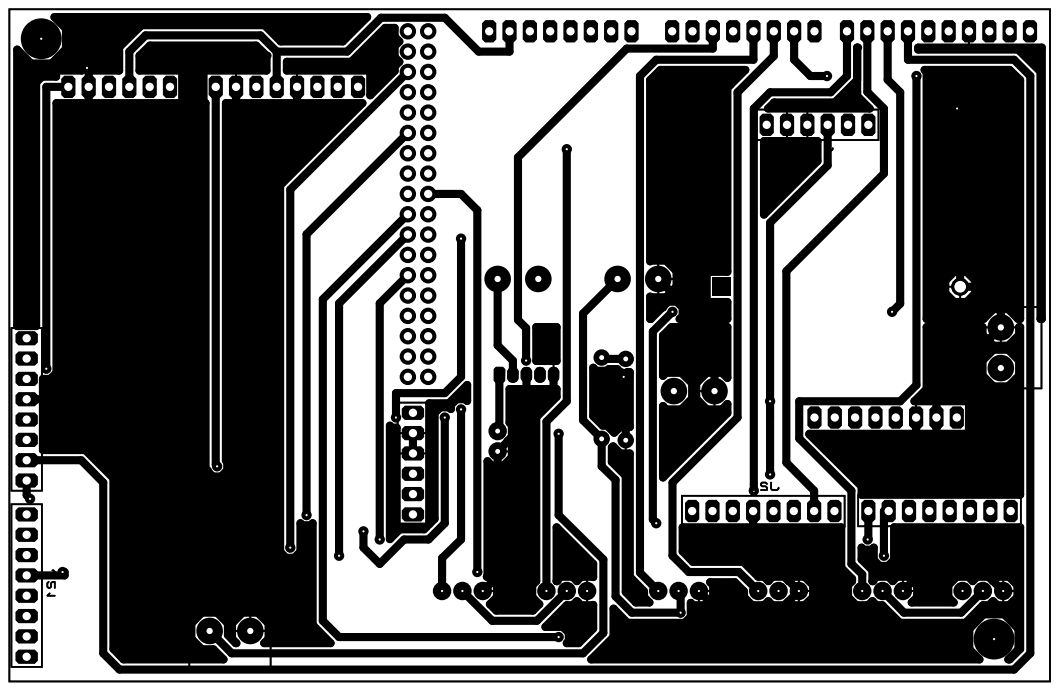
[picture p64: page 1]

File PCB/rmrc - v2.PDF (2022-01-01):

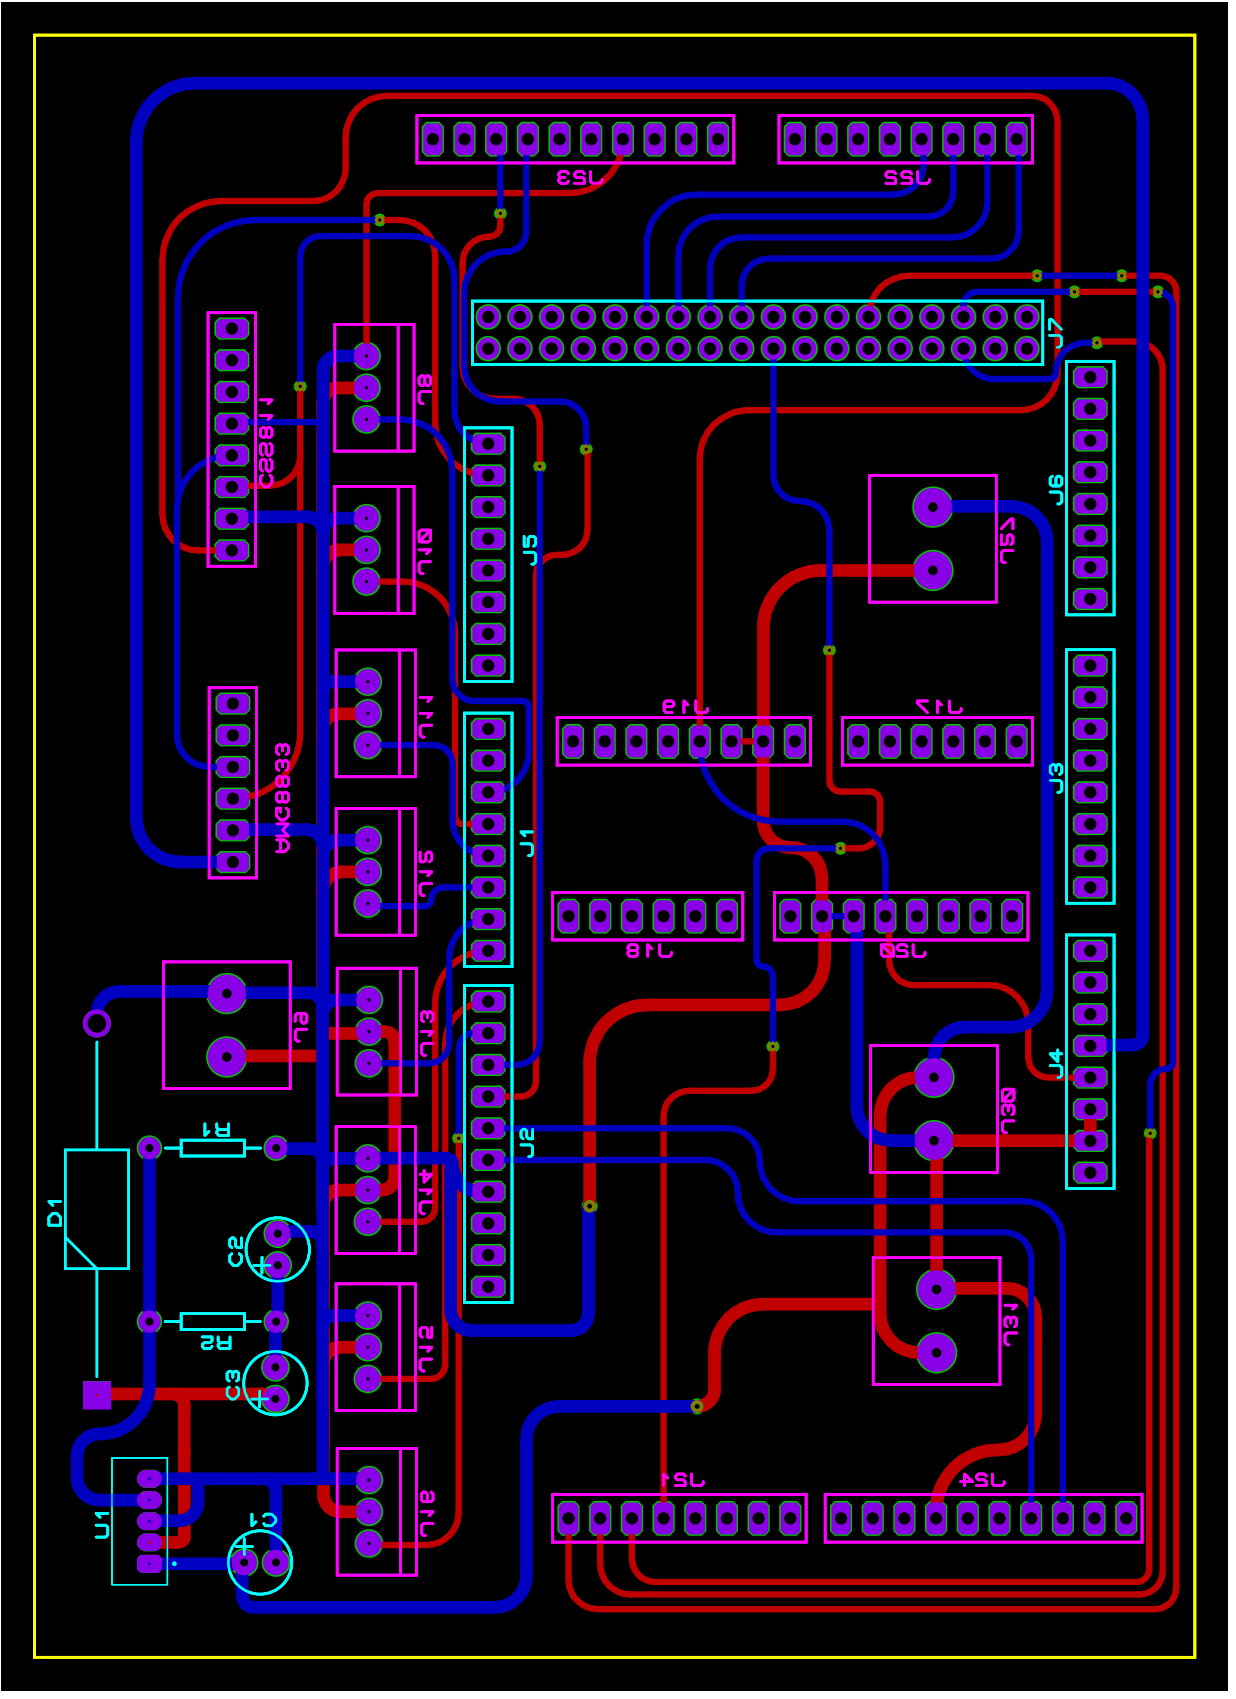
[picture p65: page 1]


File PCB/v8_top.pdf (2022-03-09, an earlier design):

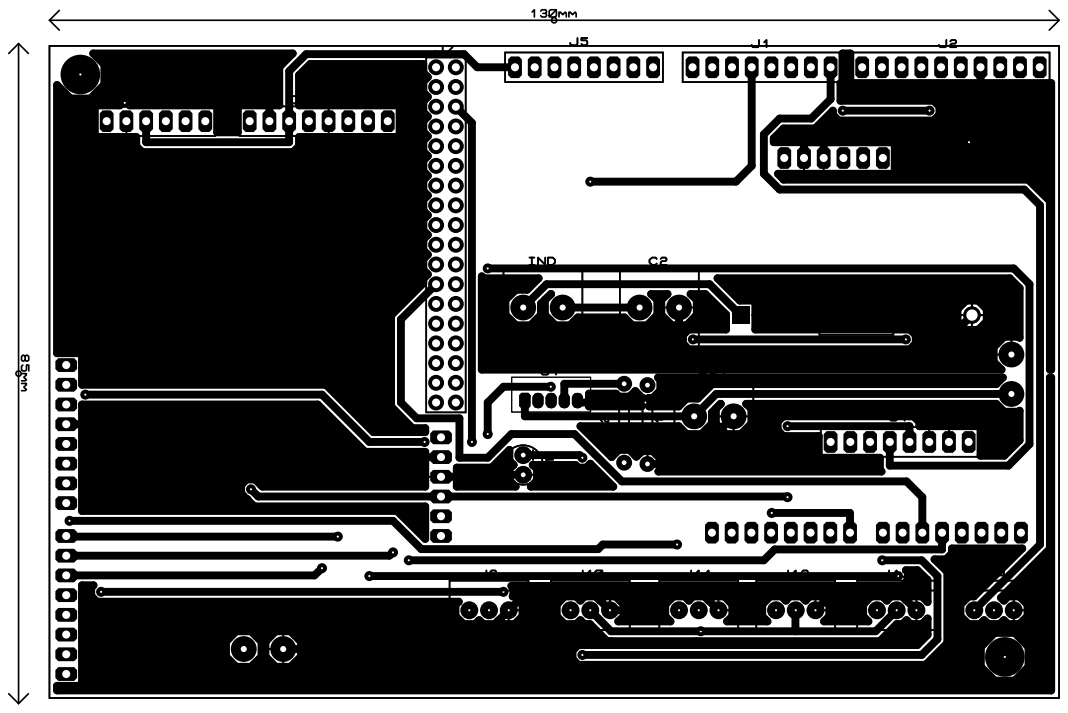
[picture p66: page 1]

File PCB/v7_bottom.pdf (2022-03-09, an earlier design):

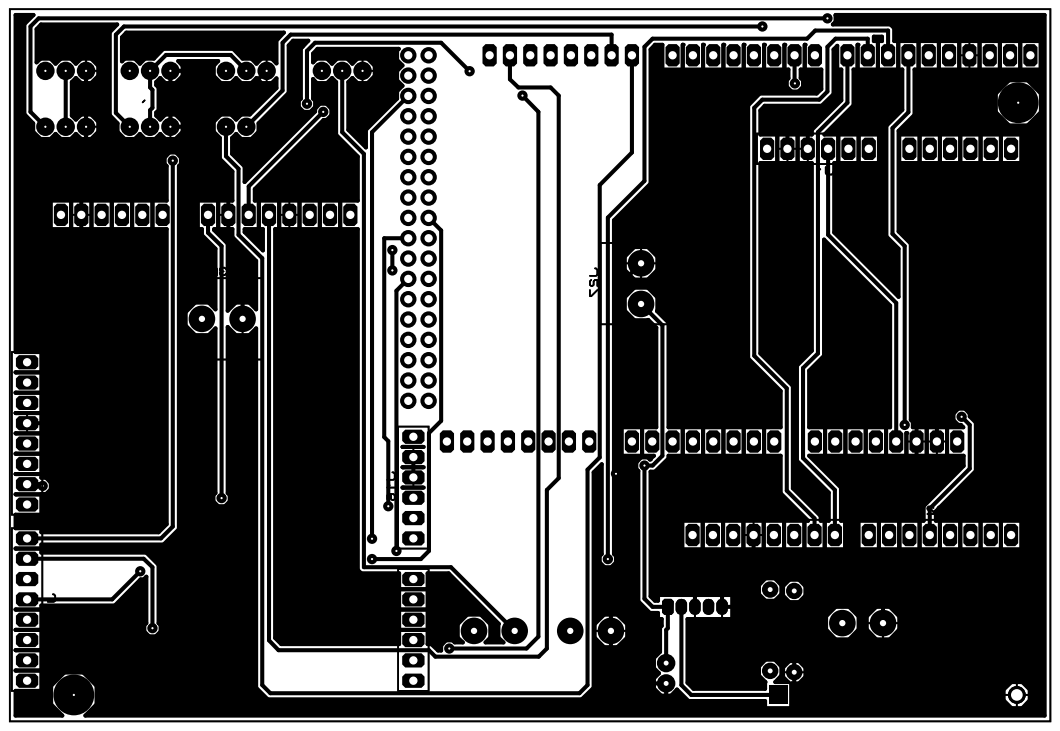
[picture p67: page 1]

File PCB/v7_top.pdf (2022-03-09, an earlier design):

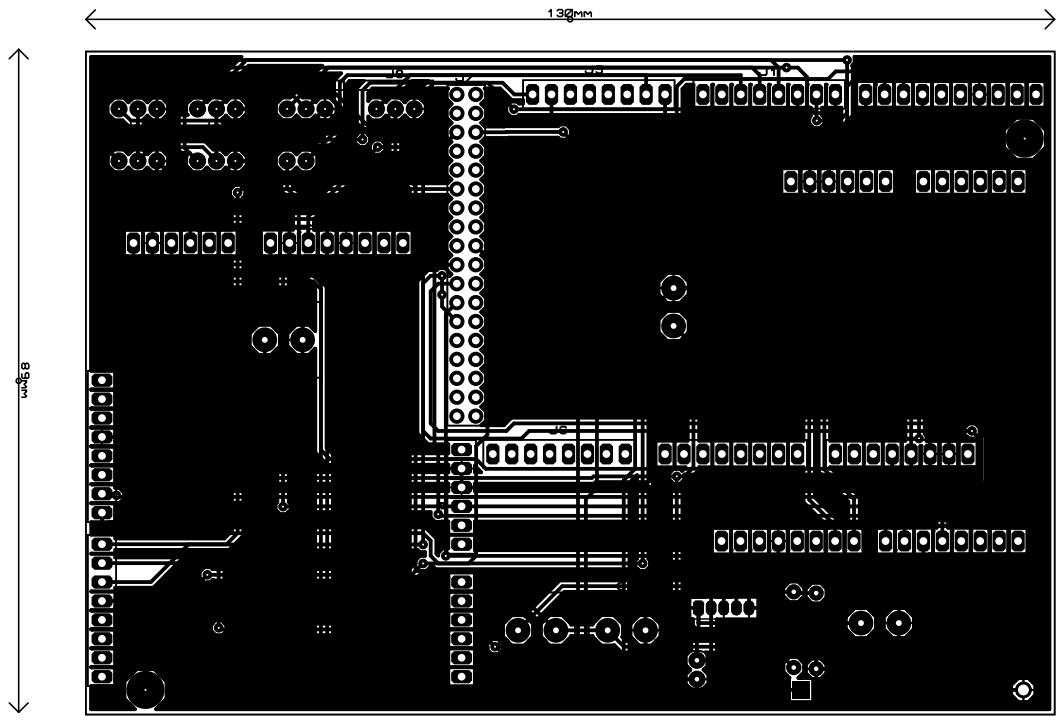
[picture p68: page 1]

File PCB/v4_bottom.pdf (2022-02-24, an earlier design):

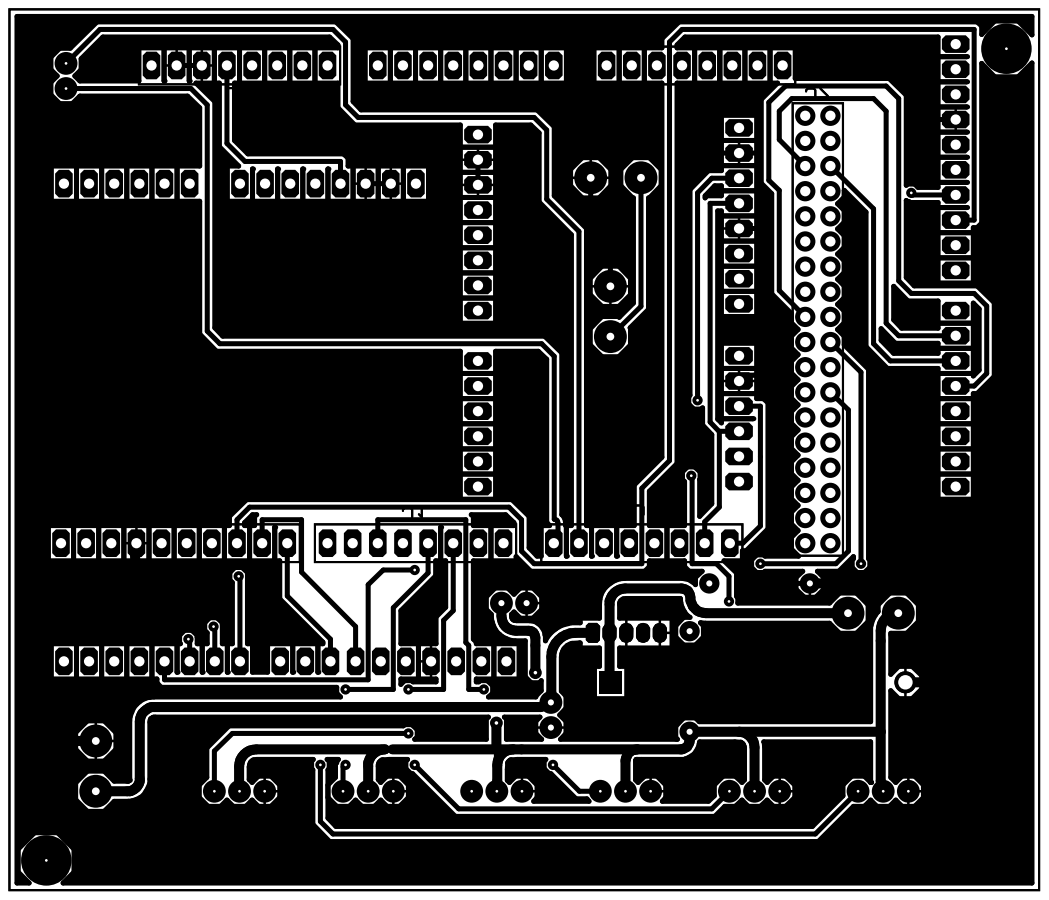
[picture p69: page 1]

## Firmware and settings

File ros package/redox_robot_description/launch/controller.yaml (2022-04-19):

redox_robot_controller:
  # Publish all joint states -----------------------------------
  joint_state_controller:
    type: joint_state_controller/JointStateController
    publish_rate: 50

  # Position Controllers --------------------------------------
  Rev1_position_controller:
    type: effort_controllers/JointPositionController
    joint: Rev1
    pid: {p: 100.0, i: 0.01, d: 10.0}
  Rev2_position_controller:
    type: effort_controllers/JointPositionController
    joint: Rev2
    pid: {p: 100.0, i: 0.01, d: 10.0}
  Rev3_position_controller:
    type: effort_controllers/JointPositionController
    joint: Rev3
    pid: {p: 100.0, i: 0.01, d: 10.0}
  Rev4_position_controller:
    type: effort_controllers/JointPositionController
    joint: Rev4
    pid: {p: 100.0, i: 0.01, d: 10.0}

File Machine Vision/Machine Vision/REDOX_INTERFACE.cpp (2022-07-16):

#include <iostream>
#include <string>
#include <opencv2/opencv.hpp>
#include "ROS_communication.h"
#include "Gamepad_controller.h"
#include "Claw.h"
#include "Thermal_gas.h"
#include "QR_read.h"
#include "Motion_detection.h"
#include "Hazmat_detection.h"
#define WHEEL_RADIUS 0.08
#define WHEELBASE 0.168
#define MAX_SPEED 0.75
using namespace std;
using namespace cv;
//Recommended resolution for monitor display: set to 1280x720
int resolution_horizontal = 800;
int resolution_vertical = 448;
int current_camera = 1;
VideoCapture capture;
VideoCapture captureClaw;
Mat webcam_image;
bool autonomous_mode = false;
bool dexterity_mode = false;
bool qr_detection = false;
bool hazmat_detection = false;
bool motion_detection = false;

void openCamera(int index)
{
	//1 = t265(front), 2 = c920(back), 3 = imx219(claw)
	if (index == 1 || index == 2)
	{
		if (captureClaw.isOpened())
			captureClaw.release();
		if (!capture.isOpened())
			capture.open(1);
		capture.set(CAP_PROP_FPS, 30);
		capture.set(CAP_PROP_CONVERT_RGB, false);
	}
	else if (index == 3)
	{
		if (capture.isOpened())
			capture.release();
		captureClaw = VideoCapture(csi_gstreamer_pipeline(1280, 720), CAP_GSTREAMER);
	}
}

void checkUserInput()
{
	UpdateServosInput();
	if (use_keyboard == false)
		UpdateGamepadInput();
	else
		UpdateKeyboardInput();
	if (gamepad_command == "previous_camera" || gamepad_command == "next_camera")
	{
		if (gamepad_command == "previous_camera")
			current_camera--;
		else if (gamepad_command == "next_camera")
			current_camera++;
		if (current_camera < 0)
			current_camera = 3;
		else if (current_camera > 3)
			current_camera = 0;
		openCamera(current_camera);
	}
	else if (gamepad_command == "autonomous_mode")
		autonomous_mode = !autonomous_mode;
	else if (gamepad_command == "dexterity_mode")
	{
		dexterity_mode = !dexterity_mode;
		cout << "DEXTERITY: " << to_string(dexterity_mode) << "\n";
		if (dexterity_mode)
			WriteArduino("ExtendClaw", 0, 0);
		else
			WriteArduino("RetractClaw", 0, 0);
	}
	else if (gamepad_command == "motion_detection")
		motion_detection = !motion_detection;
	else if (gamepad_command == "qr_detection")
		qr_detection = !qr_detection;
	else if (gamepad_command == "hazmat_detection")
		hazmat_detection = !hazmat_detection;
	else if (!servos_command.empty())
	{
		cout << servos_command << "\n";
		WriteArduino(servos_command, servos_value, 0);
	}
	else if (!autonomous_mode && !gamepad_command.empty())
	{
		if (current_camera == 2)
		{
			int temp = gamepad_value_1;	
			gamepad_value_1 = -gamepad_value_2;
			gamepad_value_2 = -temp;
		}
		cout << gamepad_command << " " << to_string(gamepad_value_1) << " " << to_string(gamepad_value_2) << "\n";
		WriteArduino(gamepad_command, gamepad_value_1, gamepad_value_2);
	} 
	else if (autonomous_mode)
	{
		float v_l = ((2 * cmdvel_linear_x) - (cmdvel_angular_z * WHEELBASE)) / (2 * WHEEL_RADIUS);
		float v_r = ((2 * cmdvel_linear_x) + (cmdvel_angular_z * WHEELBASE)) / (2 * WHEEL_RADIUS);
		int pwm_l = int(v_l * (max_pwm / MAX_SPEED));
		int pwm_r = int(v_r * (max_pwm / MAX_SPEED));
		if (current_camera == 2)
		{
			int temp = pwm_l;	
			pwm_l = -pwm_r;
			pwm_r = -temp;
		}
		cout << "(AUTONOMOUS) MotorsMove " << to_string(pwm_l) << " " << to_string(pwm_r) << "\n";
		WriteArduino("MotorsMove", pwm_l, pwm_r);
	}
}

void checkSensorsFeed()
{
	ReadArduino();
	UpdateGas(current_gas);
	UpdateThermal(current_temperature);
	if (current_camera == 1)
		webcam_image = rs_img.clone();
	else if (current_camera == 2)
		capture >> webcam_image;
	else if (current_camera == 3)
		captureClaw.read(webcam_image);
	if (current_camera == 1 || current_camera == 3)
		resize(webcam_image, webcam_image, Size(resolution_horizontal, resolution_vertical), INTER_NEAREST);
	if (qr_detection)
		webcam_image = ReadQR(webcam_image);
	if (hazmat_detection)
	{
		cout << to_string(webcam_image.dims) << endl;
		webcam_image = DetectHazmat(webcam_image);
	}
	if (motion_detection)
		webcam_image = DetectMotion(webcam_image);
}

void updateInterface()
{
	resizeWindow("REDOX", resolution_horizontal, resolution_vertical);
	imshow("REDOX", webcam_image);
	imshow("CO2", gas_image);
	imshow("Thermal", thermal_image);
}

void setup(int argc, char** argv) 
{
	system("gnome-terminal -- play '|rec --buffer 512 -d'");
	ConnectROS(argc, argv);
	namedWindow("REDOX", WINDOW_AUTOSIZE);
	namedWindow("Claw");
	namedWindow("CO2");
	namedWindow("Thermal");
	CreateServoSliders();
	openCamera(1);
	InitializeQR();
	InitializeHazmat();
}

void loop()
{
	if (SDL_NumJoysticks() < 1)
	{
		try
		{
			InitializeGamepad();
		}
		catch(const std::exception& e)
		{
			std::cerr << e.what() << '\n';
		}
	}
	checkUserInput();
	checkSensorsFeed();
	updateInterface();
	waitKey(1);
}

int main(int argc, char** argv)
{
	setup(argc, argv);
	while (true)
	{
		try
		{
			loop();
		}
		catch (const exception& e)
		{
			cout << e.what() << endl;
		}
		catch ( ros::Exception &e )
		{
			cout << e.what() << endl;
		}
		catch (const cv::Exception& e)
		{
			cout << e.what() << endl;
		}
		catch (...)
		{
			cout << "Unknown error occurred!" << endl;
		}
	}
	return 0;
}

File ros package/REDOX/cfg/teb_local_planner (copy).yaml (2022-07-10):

TebLocalPlannerROS:

 odom_topic: /camera/odom/sample
    
 # Trajectory
  
 teb_autosize: True
 dt_ref: 0.3
 dt_hysteresis: 0.1
 global_plan_overwrite_orientation: True
 max_global_plan_lookahead_dist: 1.7
 feasibility_check_no_poses: 4
    
 # Robot
         
 max_vel_x: 0.3
 max_vel_x_backwards: 0.2
 max_vel_theta: 0.3
 acc_lim_x: 0.5
 acc_lim_theta: 0.5
 min_turning_radius: 0.0
 footprint_model: # types: "point", "circular", "two_circles", "line", "polygon"
   type: "point"
   #radius: 0.2 # for type "circular"
   #line_start: [-0.3, 0.0] # for type "line"
   #line_end: [0.3, 0.0] # for type "line"
   #front_offset: 0.2 # for type "two_circles"
   #front_radius: 0.2 # for type "two_circles"
   #rear_offset: 0.2 # for type "two_circles"
   #rear_radius: 0.2 # for type "two_circles"
   #vertices: [ [0.25, -0.05], [0.18, -0.05], [0.18, -0.18], [-0.19, -0.18], [-0.25, 0], [-0.19, 0.18], [0.18, 0.18], [0.18, 0.05], [0.25, 0.05] ] # for type "polygon"

 # GoalTolerance
    
 xy_goal_tolerance: 0.2
 yaw_goal_tolerance: 0.1
 free_goal_vel: False
    
 # Obstacles
    
 min_obstacle_dist: 0.4
 include_costmap_obstacles: True
 costmap_obstacles_behind_robot_dist: 1.0
 obstacle_poses_affected: 30
 costmap_converter_plugin: "costmap_converter::CostmapToPolygonsDBSMCCH"
 costmap_converter_spin_thread: True
 costmap_converter_rate: 5

 # Optimization
    
 no_inner_iterations: 5
 no_outer_iterations: 4
 optimization_activate: True
 optimization_verbose: False
 penalty_epsilon: 0.1
 weight_max_vel_x: 2
 weight_max_vel_theta: 1
 weight_acc_lim_x: 1
 weight_acc_lim_theta: 1
 weight_kinematics_nh: 1000
 weight_kinematics_forward_drive: 0
 weight_kinematics_turning_radius: 1
 weight_optimaltime: 1
 weight_obstacle: 90
 weight_dynamic_obstacle: 10 # not in use yet
 alternative_time_cost: False # not in use yet

 # Homotopy Class Planner

 enable_homotopy_class_planning: True
 enable_multithreading: True
 simple_exploration: False
 max_number_classes: 4
 roadmap_graph_no_samples: 15
 roadmap_graph_area_width: 5
 h_signature_prescaler: 0.5
 h_signature_threshold: 0.1
 obstacle_keypoint_offset: 0.1
 obstacle_heading_threshold: 0.45
 visualize_hc_graph: False

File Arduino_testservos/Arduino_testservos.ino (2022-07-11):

#include <Servo.h>
#define basearmA_pin 6
#define basearmB_pin 7
#define forearm_pin 4
#define hand_pin 5
#define gripperTurner_pin 3
#define gripperOpener_pin 2
Servo basearmA, basearmB, forearm, hand, gripperTurner, gripperOpener;

void setup() {
  basearmA.attach(basearmA_pin);
  basearmB.attach(basearmB_pin);
  forearm.attach(forearm_pin);
  hand.attach(hand_pin);
  gripperOpener.attach(gripperOpener_pin);
  gripperTurner.attach(gripperTurner_pin);
}

void loop() {
  forearm.write(0);
  hand.write(0);
  basearmA.write(130);
  basearmB.write(50);
  gripperOpener.write(60);
  gripperTurner.write(90);
}

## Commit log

2021-10-02 Augmentation script prototype
2021-10-03 Initial arduino prototype code
2021-11-09 Motion detection prototype
2021-12-26 Arduino now interprets incoming serial data + updated 3d model
2021-12-30 arquivos pcb
2022-01-01 atualização vc pcb
2022-01-10 atualização v2 da placa, agora com zone mode em gnd nas duas faces
2022-01-10 gerber files to pcb print
    [rmrc - v2 - CADCAM Bottom Assembly.GBR, rmrc - v2 - CADCAM Bottom Copper.GBR, rmrc - v2 - CADCAM Bottom Silk Screen.GBR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]
2022-01-21 Low-pass filter for thermal and gas readings
2022-01-23 Controller inputs recognized using SDL (and registered motor pins)
2022-01-24 Write controller input on serial and terminal (missing claw control)
    [Arduino_Side.ino, Gamepad_controller.h, REDOX_INTERFACE.cpp]
2022-02-02 MoveServo(), arduino_side bug fixes,
    [Arduino_Side.ino, Gamepad_controller.h, Motors.h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]
2022-02-03 Claw show and control through interface
2022-02-04 Servo positions controlled by trackbars
2022-02-24 v4 e v5 do pcb
2022-03-07 new pcb files
    [v4_3d.dxf]
2022-03-07 placa 3d v5
    [rmrc_v5.STEP]
2022-03-09 v7 and v8 pcb layout
    [rmrv_v8.STEP]
2022-03-09 v8 from pcb
2022-03-09 adjuste on pcb v8
    [rmrv_v8.STEP]
2022-03-12 version 9 pcb finished
    [rmrv_v9.STEP]
2022-03-13 final chances pcb v9 version
    [rmrv_v9.STEP]
2022-03-15 Hazmat detector working
    [Body1.stl, Body2.stl, Body4.stl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]
2022-04-20 Updated URDF with rubber tires
    [back_camera_1.stl, redox_robot.xacro, wheel_1.stl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]
2022-04-23 bundled dependencies
    [configuration.h]
2022-04-26 Built with cmake
    [configuration.h]
2022-04-28 Updated STL files
    [Body1.stl, Body19 (Recortar 2) (Recortar 1).stl, Body19 (Recortar 2) (Recortar 2).stl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]
2022-04-29 Correct motor pins + Enable
    [Arduino_testmotors.ino, Motors.h]
2022-05-01 corrected motor directions
2022-05-02 v10 pcb and tdp
2022-05-03 Mode switch sliders
2022-05-04 spawn htop and reposition Claw/Mode windows
2022-05-08 mapping and exploration prototype
2022-05-21 V10 PCB
2022-05-23 New stl files
    [Body23_21maio (Recortar 1).stl, Body23_21maio (Recortar 2).stl, Roda.stl]
2022-06-02 Corrections to arduino_side.ino
2022-06-07 xacro lidar dummy
    [redox_robot.xacro]
2022-06-18 Final DC motor pins
2022-06-26 recompiling for ARM architecture, removed htop, added libcanberra-gtk-module to bash installer
2022-06-27 reverse controls when going backwards
    [REDOX_INTERFACE.cpp]
2022-06-28 chmod on default arduino serial port
2022-06-28 /gas and /temperature ros topics published
2022-06-28 fixed type conversion warnings on Arduino_Side
    [Arduino_Side.ino]
2022-06-29 fixed /Temperature topic out of sync
    [Arduino_Side.ino]
2022-07-01 topic changes
    [back_camera_1.stl, base_link.stl, base_scan_1.stl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]
2022-07-03 fixed movement delay bc of low baud rate
    [Arduino_Side.ino, Gamepad_controller.h, Motors.h]
2022-07-03 Fixed bug where robot would turn the wrong way when using backwards camera
    [REDOX_INTERFACE.cpp]
2022-07-03 Claw camera
2022-07-03 Arduino Sensors.h no longer remaps temperature range
    [REDOX_INTERFACE.cpp, Thermal_gas.h]
2022-07-04 Temperature colors
2022-07-05 laserscan working with odom rviz
2022-07-05 mode switch via controller buttons
2022-07-06 New noIR claw camera working
2022-07-10 Fixed realsense ros fisheye stream bugs
    [REDOX_INTERFACE.cpp]
2022-07-11 New gripperOpener servo
2022-07-11 Fixed bug where getFBRL was not called + servo constraint adjustments
    [Servos.h]
2022-07-12 URDF - right orientation
    [redox_ros.xacro]
2022-07-13 Update URDF + catkin.sh
    [redox_robot.xacro]
2022-07-13 World frame
    [redox_robot.xacro]
2022-08-31 Moved unused hazmat dataset files to K1D repository
    [yolov3-tiny.cfg]
